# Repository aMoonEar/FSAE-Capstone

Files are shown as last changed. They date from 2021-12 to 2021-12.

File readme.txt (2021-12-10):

_________________________________________________________________

FSAE2 

Team Members:
Abdalaziz AlGhoul
Hisham Ali
Hasan Shazad
Munir Alsafi
Peter Saroufim

_________________________________________________________________

How to run the parametrization:

The parametrization can be ran from the MAIN.m file found in the MATLAB folder.
Running this program in MATLAB opens the GUI. The GUI has buttons to alter the input
parameters of the vehicle, alongside a button at the bottom of the GUI to re-generate
the vehicle assembly.

On the right of the GUI is an output log of the parameters that are calculated with the 
given inputs.

Once the dialog window claiming 'Successfully optimized' is shown, please re-build the solidworks
assembly to view the optimzed vehicle.

When the parameters are generated, the main differences can be found in the following assemblies

Solidworks\Steering\Updated Steering\Steering Rack and Pinion\Rack and Pinion

Solidworks\Suspension\SubAssemblies\Shock_Absorber_Assembly
Solidworks\Suspension\SubAssemblies\FLCALeft_Assembly
Solidworks\Suspension\SubAssemblies\FLCARight_Assembly
Solidworks\Suspension\SubAssemblies\FPushrod_Assembly
Solidworks\Suspension\SubAssemblies\FUCA_Assembly
Solidworks\Suspension\SubAssemblies\RLCALeft_Assembly
Solidworks\Suspension\SubAssemblies\RLCARight_Assembly
Solidworks\Suspension\SubAssemblies\RPushrod_Assembly

Solidworks\Chassis with Panels

_________________________________________________________________

Locations of Files:

[GroupFSAE2]
--> Log: Contains the output log while generating the updated design of the vehicle

--> MATLAB: Contains all of the programming code
-----> MAIN.m: Main matlab file that runs the GUI
-----> Subfunctions: Contains subfunctions that are used within the MAIN.m file

--> Reports: Contains all past written reports alongside the overleaf zips

--> Solidworks: Contains the main assembly and sub-assemblies
-----> Assembly.SLDASM: Main Vehicle assembly that gets updated with the parameters
-----> Equations: Contains the equation and parameters used in the solidworks parts
-----> Rest of the folders: Contains the subassemblies and parts

--> Excel Modelling: Contains the excel sheets used to model the vehicle

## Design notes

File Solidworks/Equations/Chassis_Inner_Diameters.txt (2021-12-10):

"Front_Hoop_ID"= 22.5mm

"D2@Sketch15"="Front_Hoop_ID"

"Front_Bulkhead_IW"= 22.2mm

"D4@Sketch18"="Front_Bulkhead_IW"

"Front_Bulkhead_SupportLower_IW"= 22.2mm

"D3@Sketch2"="Front_Bulkhead_SupportLower_IW"

"Front_Bulkhead_Bracing_ID"= 23mm

"D2@Sketch1"="Front_Bulkhead_Bracing_ID"

"D2@Sketch110"="Front_Bulkhead_Bracing_ID"

"Front_Bulkhead_Support_ID"= 23mm

"Side_Impact_Structure_ID"= 22.2mm

"D4@Sketch116" = "Side_Impact_Structure_ID"

"D2@Sketch119" = "Side_Impact_Structure_ID"

"Main_Hoop_Bracing_ID"= 23mm

"D2@Sketch120"="Main_Hoop_Bracing_ID"

"D2@Sketch121"="Main_Hoop_Bracing_ID"

"Rear_Bulkhead_ID"= 22.2mm

"D4@Sketch122"="Rear_Bulkhead_ID"

"D2@Sketch123"="Rear_Bulkhead_ID"

"Main_Hoop_ID"= 22.5mm

"D2@Sketch125"="Main_Hoop_ID"

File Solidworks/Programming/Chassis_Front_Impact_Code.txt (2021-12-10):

format long;

%Problem Characteristics
nnode = 18;                 %Number of Nodes
ndof_per_node = 3;          %Number of degrees of freedom per node
nnode_per_element = 2;      %Number of nodes per elements
nelem = 32;                 %Number of elements
nmat = 1;                   %Number of material types

%Elastic Modulus and Yield Stress of 4130 AISI Steel Tubes
Elastic_modulus = zeros(nmat,1);
Elastic_modulus(1,1) =  205000; %MPa

%Shear Modulus
Shear_modulus = zeros(nmat,1);
Shear_modulus(1,1) = 80000; %MPa

%Nodal coordinates in milimeters
Nodal_coordinates = zeros (nnode,2);

    %First line is the nodal coordinate is the x coordinate
    %Second line is the nodal coordinate is the y coordinate

Nodal_coordinates(1,1) = 0;
Nodal_coordinates(1,2) = 0;

Nodal_coordinates(2,1) = 0;
Nodal_coordinates(2,2) = 340;

Nodal_coordinates(3,1) = 439;
Nodal_coordinates(3,2) = 0;

Nodal_coordinates(4,1) = 451.66;
Nodal_coordinates(4,2) = 230;

Nodal_coordinates(5,1) = 463.78;
Nodal_coordinates(5,2) = 460.18;

Nodal_coordinates(6,1) = 878;
Nodal_coordinates(6,2) = 597.38;

Nodal_coordinates(7,1) = 878;
Nodal_coordinates(7,2) = 575.83;

Nodal_coordinates(8,1) = 878;
Nodal_coordinates(8,2) = 277;

Nodal_coordinates(9,1) = 878;
Nodal_coordinates(9,2) = 0;

Nodal_coordinates(10,1) = 1357;
Nodal_coordinates(10,2) = -51.5;

Nodal_coordinates(11,1) = 1836;
Nodal_coordinates(11,2) = -103;

Nodal_coordinates(12,1) = 1836;
Nodal_coordinates(12,2) = 275;

Nodal_coordinates(13,1) = 1836;
Nodal_coordinates(13,2) = 327.09;

Nodal_coordinates(14,1) = 1836;
Nodal_coordinates(14,2) = 1076;

Nodal_coordinates(15,1) = 2250.37;
Nodal_coordinates(15,2) = 276.37;

Nodal_coordinates(16,1) = 2249;
Nodal_coordinates(16,2) = -29;

Nodal_coordinates(17,1) = 2520;
Nodal_coordinates(17,2) = -29;

Nodal_coordinates(18,1) = 2520;
Nodal_coordinates(18,2) = 275;

%Connectivity table indicated the nodes that belong to each element
Connect_table = zeros(nelem,nnode_per_element + 1);

    %First line is node i that belongs to the element
    %Second line is node j that belongs to the element
    %Third line is the material flag
    
Connect_table(1,1) = 1;
Connect_table(1,2) = 2;
Connect_table(1,3) = 1;

Connect_table(2,1) = 2;
Connect_table(2,2) = 5;
Connect_table(2,3) = 1;

Connect_table(3,1) = 2;
Connect_table(3,2) = 4;
Connect_table(3,3) = 1;

Connect_table(4,1) = 1;
Connect_table(4,2) = 4;
Connect_table(4,3) = 1;

Connect_table(5,1) = 1;
Connect_table(5,2) = 3;
Connect_table(5,3) = 1;

Connect_table(6,1) = 5;
Connect_table(6,2) = 4;
Connect_table(6,3) = 1;

Connect_table(7,1) = 4;
Connect_table(7,2) = 3;
Connect_table(7,3) = 1;

Connect_table(8,1) = 5;
Connect_table(8,2) = 7;
Connect_table(8,3) = 1;

Connect_table(9,1) = 4;
Connect_table(9,2) = 7;
Connect_table(9,3) = 1;

Connect_table(10,1) = 4;
Connect_table(10,2) = 8;
Connect_table(10,3) = 1;

Connect_table(11,1) = 4;
Connect_table(11,2) = 9;
Connect_table(11,3) = 1;

Connect_table(12,1) = 3;
Connect_table(12,2) = 9;
Connect_table(12,3) = 1;

Connect_table(13,1) = 7;
Connect_table(13,2) = 6;
Connect_table(13,3) = 1;

Connect_table(14,1) = 7;
Connect_table(14,2) = 8;
Connect_table(14,3) = 1;

Connect_table(15,1) = 8;
Connect_table(15,2) = 9;
Connect_table(15,3) = 1;

Connect_table(16,1) = 7;
Connect_table(16,2) = 12;
Connect_table(16,3) = 1;

Connect_table(17,1) = 8;
Connect_table(17,2) = 12;
Connect_table(17,3) = 1;

Connect_table(18,1) = 9;
Connect_table(18,2) = 12;
Connect_table(18,3) = 1;

Connect_table(19,1) = 9;
Connect_table(19,2) = 10;
Connect_table(19,3) = 1;

Connect_table(20,1) = 10;
Connect_table(20,2) = 11;
Connect_table(20,3) = 1;

Connect_table(21,1) = 11;
Connect_table(21,2) = 12;
Connect_table(21,3) = 1;

Connect_table(22,1) = 12;
Connect_table(22,2) = 13;
Connect_table(22,3) = 1;

Connect_table(23,1) = 13;
Connect_table(23,2) = 14;
Connect_table(23,3) = 1;

Connect_table(24,1) = 14;
Connect_table(24,2) = 15;
Connect_table(24,3) = 1;

Connect_table(25,1) = 12;
Connect_table(25,2) = 15;
Connect_table(25,3) = 1;

Connect_table(26,1) = 11;
Connect_table(26,2) = 15;
Connect_table(26,3) = 1;

Connect_table(27,1) = 11;
Connect_table(27,2) = 16;
Connect_table(27,3) = 1;

Connect_table(28,1) = 15;
Connect_table(28,2) = 16;
Connect_table(28,3) = 1;

Connect_table(29,1) = 16;
Connect_table(29,2) = 17;
Connect_table(29,3) = 1;

Connect_table(30,1) = 15;
Connect_table(30,2) = 17;
Connect_table(30,3) = 1;

Connect_table(31,1) = 15;
Connect_table(31,2) = 18;
Connect_table(31,3) = 1;

Connect_table(32,1) = 17;
Connect_table(32,2) = 18;
Connect_table(32,3) = 1;

%Radii of tubes in mm
OutterradiustubeA = 12.5;
InnerradiustubeA = (12.5 - 1.25)-4;

OutterradiustubeB = 12.7;
InnerradiustubeB = (12.7 - 1.6);

%Width of sqaure tubes in mm
OutterWidthtubeB = 25.4;
InnerWidthtubeB = (25.4-3.2)-4;

%Moment of inertia of tubes (I)
InertiaPipeA = (pi/4)*((OutterradiustubeA^4)-(InnerradiustubeA^4));
InertiaPipeB = (pi/4)*((OutterradiustubeB^4)-(InnerradiustubeB^4));
InertiaSquareB = ((OutterWidthtubeB^4)/12)-((InnerWidthtubeB^4)/12);

%Polar moment of inertia of tubes (J)
PolarpipeA = (pi/2)*((OutterradiustubeA^4)-(InnerradiustubeA^4));
PolarpipeB = (pi/2)*((OutterradiustubeB^4)-(InnerradiustubeB^4));
PolarsquareB = ((OutterWidthtubeB^4)/6)-((InnerWidthtubeB^4)/6);

%Assigning an outer radius to each element
Tube_outer_radius = zeros(nelem,nmat);
Tube_outer_radius(1,1) = OutterradiustubeB;
Tube_outer_radius(2,1) = OutterradiustubeB;
Tube_outer_radius(3,1) = OutterradiustubeB;
Tube_outer_radius(4,1) = OutterradiustubeB;
Tube_outer_radius(5,1) = OutterWidthtubeB;
Tube_outer_radius(6,1) = OutterradiustubeB;
Tube_outer_radius(7,1) = OutterradiustubeB;
Tube_outer_radius(8,1) = OutterradiustubeB;
Tube_outer_radius(9,1) = OutterradiustubeB;
Tube_outer_radius(10,1) = OutterradiustubeB;
Tube_outer_radius(11,1) = OutterradiustubeB;
Tube_outer_radius(12,1) = OutterWidthtubeB;
Tube_outer_radius(13,1) = OutterradiustubeA;
Tube_outer_radius(14,1) = OutterradiustubeA;
Tube_outer_radius(15,1) = OutterradiustubeA;
Tube_outer_radius(16,1) = OutterradiustubeB;
Tube_outer_radius(17,1) = OutterradiustubeB;
Tube_outer_radius(18,1) = OutterradiustubeB;
Tube_outer_radius(19,1) = OutterWidthtubeB;
Tube_outer_radius(20,1) = OutterWidthtubeB;
Tube_outer_radius(21,1) = OutterradiustubeA;
Tube_outer_radius(22,1) = OutterradiustubeA;
Tube_outer_radius(23,1) = OutterradiustubeA;
Tube_outer_radius(24,1) = OutterradiustubeB;
Tube_outer_radius(25,1) = OutterradiustubeB;
Tube_outer_radius(26,1) = OutterradiustubeB;
Tube_outer_radius(27,1) = OutterWidthtubeB;
Tube_outer_radius(28,1) = OutterradiustubeB;
Tube_outer_radius(29,1) = OutterWidthtubeB;
Tube_outer_radius(30,1) = OutterradiustubeB;
Tube_outer_radius(31,1) = OutterradiustubeB;
Tube_outer_radius(32,1) = OutterradiustubeB;

%Assigning an inner radius to each element
Tube_inner_radius = zeros(nelem,nmat);
Tube_inner_radius(1,1) = InnerradiustubeB;
Tube_inner_radius(2,1) = InnerradiustubeB;
Tube_inner_radius(3,1) = InnerradiustubeB;
Tube_inner_radius(4,1) = InnerradiustubeB;
Tube_inner_radius(5,1) = InnerWidthtubeB;
Tube_inner_radius(6,1) = InnerradiustubeB;
Tube_inner_radius(7,1) = InnerradiustubeB;
Tube_inner_radius(8,1) = InnerradiustubeB;
Tube_inner_radius(9,1) = InnerradiustubeB;
Tube_inner_radius(10,1) = InnerradiustubeB;
Tube_inner_radius(11,1) = InnerradiustubeB;
Tube_inner_radius(12,1) = InnerWidthtubeB;
Tube_inner_radius(13,1) = InnerradiustubeA;
Tube_inner_radius(14,1) = InnerradiustubeA;
Tube_inner_radius(15,1) = InnerradiustubeA;
Tube_inner_radius(16,1) = InnerradiustubeB;
Tube_inner_radius(17,1) = InnerradiustubeB;
Tube_inner_radius(18,1) = InnerradiustubeB;
Tube_inner_radius(19,1) = InnerWidthtubeB;
Tube_inner_radius(20,1) = InnerWidthtubeB;
Tube_inner_radius(21,1) = InnerradiustubeA;
Tube_inner_radius(22,1) = InnerradiustubeA;
Tube_inner_radius(23,1) = InnerradiustubeA;
Tube_inner_radius(24,1) = InnerradiustubeB;
Tube_inner_radius(25,1) = InnerradiustubeB;
Tube_inner_radius(26,1) = InnerradiustubeB;
Tube_inner_radius(27,1) = InnerWidthtubeB;
Tube_inner_radius(28,1) = InnerradiustubeB;
Tube_inner_radius(29,1) = InnerWidthtubeB;
Tube_inner_radius(30,1) = InnerradiustubeB;
Tube_inner_radius(31,1) = InnerradiustubeB;
Tube_inner_radius(32,1) = InnerradiustubeB;

%Assigning a moment of inertia to every element
Tube_inertia = zeros(nelem,nmat);
Tube_inertia(1,1) = InertiaPipeB;
Tube_inertia(2,1) = InertiaPipeB;
Tube_inertia(3,1) = InertiaPipeB;
Tube_inertia(4,1) = InertiaPipeB;
Tube_inertia(5,1) = InertiaSquareB;
Tube_inertia(6,1) = InertiaPipeB;
Tube_inertia(7,1) = InertiaPipeB;
Tube_inertia(8,1) = InertiaPipeB;
Tube_inertia(9,1) = InertiaPipeB;
Tube_inertia(10,1) = InertiaPipeB;
Tube_inertia(11,1) = InertiaPipeB;
Tube_inertia(12,1) = InertiaSquareB;
Tube_inertia(13,1) = InertiaPipeA;
Tube_inertia(14,1) = InertiaPipeA;
Tube_inertia(15,1) = InertiaPipeA;
Tube_inertia(16,1) = InertiaPipeB;
Tube_inertia(17,1) = InertiaPipeB;
Tube_inertia(18,1) = InertiaPipeB;
Tube_inertia(19,1) = InertiaSquareB;
Tube_inertia(20,1) = InertiaSquareB;
Tube_inertia(21,1) = InertiaPipeA;
Tube_inertia(22,1) = InertiaPipeA;
Tube_inertia(23,1) = InertiaPipeA;
Tube_inertia(24,1) = InertiaPipeB;
Tube_inertia(25,1) = InertiaPipeB;
Tube_inertia(26,1) = InertiaPipeB;
Tube_inertia(27,1) = InertiaSquareB;
Tube_inertia(28,1) = InertiaPipeB;
Tube_inertia(29,1) = InertiaSquareB;
Tube_inertia(30,1) = InertiaPipeB;
Tube_inertia(31,1) = InertiaPipeB;
Tube_inertia(32,1) = InertiaPipeB;

%Assigning a polar moment of inertia to every element
Tube_polar = zeros(nelem,nmat);
Tube_polar(1,1) = PolarpipeB;
Tube_polar(2,1) = PolarpipeB;
Tube_polar(3,1) = PolarpipeB;
Tube_polar(4,1) = PolarpipeB;
Tube_polar(5,1) = PolarsquareB;
Tube_polar(6,1) = PolarpipeB;
Tube_polar(7,1) = PolarpipeB;
Tube_polar(8,1) = PolarpipeB;
Tube_polar(9,1) = PolarpipeB;
Tube_polar(10,1) = PolarpipeB;
Tube_polar(11,1) = PolarpipeB;
Tube_polar(12,1) = PolarsquareB;
Tube_polar(13,1) = PolarpipeA;
Tube_polar(14,1) = PolarpipeA;
Tube_polar(15,1) = PolarpipeA;
Tube_polar(16,1) = PolarpipeB;
Tube_polar(17,1) = PolarpipeB;
Tube_polar(18,1) = PolarpipeB;
Tube_polar(19,1) = PolarsquareB;
Tube_polar(20,1) = PolarsquareB;
Tube_polar(21,1) = PolarpipeA;
Tube_polar(22,1) = PolarpipeA;
Tube_polar(23,1) = PolarpipeA;
Tube_polar(24,1) = PolarpipeB;
Tube_polar(25,1) = PolarpipeB;
Tube_polar(26,1) = PolarpipeB;
Tube_polar(27,1) = PolarsquareB;
Tube_polar(28,1) = PolarpipeB;
Tube_polar(29,1) = PolarsquareB;
Tube_polar(30,1) = PolarpipeB;
Tube_polar(31,1) = PolarpipeB;
Tube_polar(32,1) = PolarpipeB;

%Local stiffness matrices
Keloc = Local_stiffness(Nodal_coordinates,Connect_table,Tube_outer_radius,Tube_inner_radius,Tube_inertia,Tube_polar,Elastic_modulus,Shear_modulus);

%Rotation matrices to switch between local and global coordinates
R = Rotation(Nodal_coordinates,Connect_table);

%Global stiffness matrices
Ke = Global_stiffness(Keloc,R);

%Assemblage matrix
Ka = Assemblage_matrix(nnode,ndof_per_node,Connect_table,Ke);

%External force vector
Fa = zeros(nnode*ndof_per_node,1);

Frontimpact = -18245.833; %Newtons
Fa(1,1) = (Frontimpact/4);
Fa(4,1) = (Frontimpact/4);

%Gravitational Force from Driver
Fa(29,1) = 100*9.8;
Fa(32,1) = 100*9.8;

%Boundary conditions appropiate for a front impact test
BC = zeros(nnode,ndof_per_node);

%fix the rear bulkhead, 1 means fixed
BC(17,1:3) = 1;
BC(18,1:3) = 1;

% Modifying Ka into KaSol and Fa into FaSol to get solution 
  beta = max(max(Ka))*10e9;
  KaSol = Ka;
  FaSol = Fa;
  for i = 1:nnode
    for j = 1:ndof_per_node
      if BC(i,j) == 1
        KaSol((i-1)*ndof_per_node + j,(i-1)*ndof_per_node + j) = Ka((i-1)*ndof_per_node + j,(i-1)*ndof_per_node + j) + beta;
        FaSol((i-1)*ndof_per_node + j,1) = beta*0;
      end
    end
  end

%Global displacement calculation

U = KaSol\FaSol;

%Processing of result
Reaction_forces = [];
Ulocal = zeros(2*ndof_per_node,nelem);
Uglobal = zeros(2*ndof_per_node,nelem);
Flocal = zeros(2*ndof_per_node,nelem);
axial_stress = zeros(nelem,1);

Ua = U;
Fa = Ka*Ua;
x = 1;
for i = 1:nnode
    for j = 1:ndof_per_node
        if BC(i,j)==1
            Reaction_forces(x,1) = Fa((i-1)*ndof_per_node + j,1);
            x = x+1;
        end
    end
end

%Parameters to be used when calcu lating the stiffness matrices
A = Cross_sectional_of_element(Tube_outer_radius,Tube_inner_radius);
L = Length_of_elements(Nodal_coordinates,Connect_table);
E = Elastic_modulus_of_elements(Elastic_modulus,Connect_table);
G = Shear_modulus_of_elements(Shear_modulus,Connect_table);
I = Moment_Inertia_of_elements(Tube_inertia);
J = Polar_moment_of_inertia(Tube_polar);
Kglobal = Global_stiffness(Keloc,R);
%Rotating local displacement and external force vectors to global coordinates
for i = 1:nelem     
     Rot = R(:,:,i);
     for j = 1:ndof_per_node
       Uglobal(j,i) = Ua((Connect_table(i,1) - 1)*ndof_per_node + j,1);
       Uglobal(ndof_per_node + j,i) = Ua((Connect_table(i,2) - 1)*ndof_per_node + j,1);  
     end
     Ulocal(:,i) = Rot*Uglobal(:,i);
     Flocal(:,i) = Keloc(:,:,i)*Ulocal(:,i);
    %calculating stresses in each element
    axial_stress(i,1) = max(Flocal(2,i))/A(i,1); %axial stress
    shear_stress_yaxis(i,1) = (max(Flocal(1,i)))/A(i,1); %y axis shear stress
    torsional_stress(i,1) = (max(Flocal(3,i))*Tube_outer_radius(i,1))/Tube_polar(i,1); %Torsional stress
    bending_stress_yaxis(i,1) = (max(Flocal(3,i))*Tube_outer_radius(i,1))/Tube_inertia(i,1); %Bending stress y axis
end

%Oraganizing required stresses in a vector
stresses = zeros(1,4);

stresses(1,1) = max(axial_stress); %Tensile stress
stresses(1,2) = max(abs(shear_stress_yaxis(i,1))); %x Shear stress
stresses(1,3) = max(abs(torsional_stress(i,1))); %Torsional stress
stresses(1,4) = max(abs(bending_stress_yaxis(i,1))); %z Bending stress

%Calculating safety factors and organizing in a vector
SF = zeros(1,4);

SF(1,1) = abs(435/(stresses(1,1))); %Axial stress safety factor
SF(1,2) = 435/stresses(1,2); %Y Shear Stress safety factor
SF(1,3) = 435/stresses(1,3); %Torsional Stress safety factor
SF(1,4) = 435/stresses(1,4); %Y Bending Stress safety factor

disp(min(SF));

%Calculating the parameter that are used to calculate the stiffness matrix
%Area of element calculation
function A = Cross_sectional_of_element(Tube_outer_radius,Tube_inner_radius)
    [nelem,~] = size(Tube_inner_radius);
    A = zeros(nelem,1);
    for i = 1:nelem
        A(i,1) = pi*((Tube_outer_radius(i,1)^2)-(Tube_inner_radius(i,1)^2));
    end
end

function L = Length_of_elements(Nodal_coordinates,Connect_table)
    [nelem,~] = size(Connect_table);
    L = zeros(nelem,1);
    for i = 1:nelem
        L(i,1) = sqrt((Nodal_coordinates(Connect_table(i,1),1) - Nodal_coordinates(Connect_table(i,2),1))^2 + (Nodal_coordinates(Connect_table(i,1),2) - Nodal_coordinates(Connect_table(i,2),2))^2);
    end
end

%Elastic modulus of elements
function E = Elastic_modulus_of_elements(Elastic_modulus,Connect_table)
    [nelem,~] = size(Connect_table);
    E = zeros(nelem,1);
   for i = 1:nelem
    E(i,1) = Elastic_modulus(1,1);
   end
end

%Shear modulus of elements
function G = Shear_modulus_of_elements(Shear_modulus,Connect_table)
    [nelem,~] = size(Connect_table);
    G = zeros(nelem,1);
    for i = 1:nelem
    G(i,1) = Shear_modulus(1,1);
   end 
end

%Moment of inertia of elements
function I = Moment_Inertia_of_elements(Tube_inertia)
    [nelem,~] = size(Tube_inertia);
    I = zeros(nelem,1);
    for i = 1:nelem
            I(i,1) = Tube_inertia(i,1);
     end
end

%Polar moment of Inertia of elements
function J = Polar_moment_of_inertia(Tube_polar)
    [nelem,~] = size(Tube_polar);
    J = zeros(nelem,1);
    for i = 1:nelem
            J(i,1) = Tube_polar(i,1);
     end
end

%3D Local stiffness matrix calculation
function Keloc = Local_stiffness(Nodal_coordinates,Connect_table,Tube_outer_radius,Tube_inner_radius,Tube_inertia,Tube_polar,Elastic_modulus,Shear_modulus)
    [nelem,~] = size(Connect_table);
    Keloc = zeros(6,6,nelem); %each element is characterized by a 12x12 matrix
   
    A = Cross_sectional_of_element(Tube_outer_radius,Tube_inner_radius);
    L = Length_of_elements(Nodal_coordinates,Connect_table);
    E = Elastic_modulus_of_elements(Elastic_modulus,Connect_table);
    G = Shear_modulus_of_elements(Shear_modulus,Connect_table);
    I = Moment_Inertia_of_elements(Tube_inertia);
    J = Polar_moment_of_inertia(Tube_polar);
    
    for i = 1:nelem
       
        %first row
    Keloc(1,1,i) = (A(i,1)*E(i,1))/L(i,1);
    Keloc(1,4,i) = -(A(i,1)*E(i,1))/L(i,1);  
   
    %second row
    Keloc(2,2,i) = (12*E(i,1)*I(i,1))/L(i,1)^3;
    Keloc(2,3,i) = (6*E(i,1)*I(i,1))/L(i,1)^2;
    Keloc(2,5,i) = -Keloc(2,2,i);
    Keloc(2,6,i) = Keloc(2,3,i);
    
    %third row
    Keloc(3,2,i) = (6*E(i,1)*I(i,1))/L(i,1)^2;
    Keloc(3,3,i) = (4*E(i,1)*I(i,1))/L(i,1);
    Keloc(3,5,i) = -Keloc(3,2,i);
    Keloc(3,6,i) = Keloc(3,3,i)/2;
    
    %fourth row
    Keloc(4,1,i) = -(A(i,1)*E(i,1))/L(i,1);
    Keloc(4,4,i) = (A(i,1)*E(i,1))/L(i,1);
    
    %fifth row
    Keloc(5,2,i) = -(12*E(i,1)*I(i,1))/L(i,1)^3;
    Keloc(5,3,i) = -(6*E(i,1)*I(i,1))/L(i,1)^2;
    Keloc(5,5,i) = -Keloc(6,2,i);
    Keloc(5,6,i) = Keloc(6,3,i);
    
    %sixth row
    Keloc(6,2,i) = (6*E(i,1)*I(i,1))/L(i,1)^2;
    Keloc(6,3,i) = (2*E(i,1)*I(i,1))/L(i,1);
    Keloc(6,5,i) = -Keloc(3,2,i);
    Keloc(6,6,i) = Keloc(3,3,i)*2;
    end
end

function R = Rotation(Nodal_coordinates,Connect_table)
  [nelem,~] = size(Connect_table);
  R = zeros(6,6,nelem);
  L = Length_of_elements(Nodal_coordinates,Connect_table);
  for i = 1:nelem
    %l
    R(1,1,i) = (Nodal_coordinates(Connect_table(i,2),1) - Nodal_coordinates(Connect_table(i,1),1)/L(i,1));
    %m
    R(1,2,i) = (Nodal_coordinates(Connect_table(i,2),2) - Nodal_coordinates(Connect_table(i,1),2)/L(i,1));
    R(2,1,i) = -R(1,2,i);
    R(2,2,i) = R(1,1,i);
    R(3,3,i) = 1;   
    R(4,4,i) = R(1,1,i);
    R(4,5,i) = R(1,2,i);
    R(5,4,i) = -R(1,2,i);
    R(5,5,i) = R(1,1,i);
    R(6,6,i) = 1;
    R(:,:,i) = R(:,:,i)/L(i,1);     
  end
end

%Global stiffness matrix calculation
function Kglobal = Global_stiffness(Keloc,R)
    [sizeKglobal,~,nelem]=size(Keloc);
    Kglobal = zeros(sizeKglobal,sizeKglobal,nelem);
    for i = 1:nelem
        Rotate = R(:,:,i);
        Kglobal(:,:,i) = Rotate'*Keloc(:,:,i)*Rotate;
    end
end

function Ka =  Assemblage_matrix(nnode,ndof_per_node,Connect_table,Kglobal)
    Ka = zeros(nnode*ndof_per_node,nnode*ndof_per_node);
    [~,~,nelem]=size(Kglobal);
     for ii = 1:nnode
        for jj = 1:nnode
            for k = 1:nelem
                if ii == Connect_table(k,1) && jj == Connect_table(k,1)
                    for i = 1:ndof_per_node
                        for j = 1:ndof_per_node
                            Ka((ii - 1)*ndof_per_node + i,(jj - 1)*ndof_per_node + j) = Ka((ii - 1)*ndof_per_node + i,(jj - 1)*ndof_per_node + j) + Kglobal(i,j,k);
                        end
                    end
                elseif ii == Connect_table(k,2) && jj == Connect_table(k,2)
                    for i = 1:ndof_per_node
                        for j = 1:ndof_per_node
                            Ka((ii - 1)*ndof_per_node + i,(jj - 1)*ndof_per_node + j) = Ka((ii - 1)*ndof_per_node + i,(jj - 1)*ndof_per_node + j) + Kglobal(i + ndof_per_node,j + ndof_per_node,k);
                        end
                    end
                elseif ii == Connect_table(k,1) && jj == Connect_table(k,2)
                    for i = 1:ndof_per_node
                        for j = 1:ndof_per_node
                            Ka((ii - 1)*ndof_per_node + i,(jj - 1)*ndof_per_node + j) = Ka((ii - 1)*ndof_per_node + i,(jj - 1)*ndof_per_node + j) + Kglobal(i,j + ndof_per_node,k);
                        end
                    end
                elseif ii == Connect_table(k,2) && jj == Connect_table(k,1)
                    for i = 1:ndof_per_node
                        for j = 1:ndof_per_node
                            Ka((ii - 1)*ndof_per_node + i,(jj - 1)*ndof_per_node + j) = Ka((ii - 1)*ndof_per_node + i,(jj - 1)*ndof_per_node + j) + Kglobal(i + ndof_per_node,j,k);
                        end
                    end
                end
            end
        end            
     end
end

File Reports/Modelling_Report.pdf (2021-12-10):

# MCG 4322[A]

# FSAE Modelling Report

# FSAE 2

by

### AbdalAziz AlGhoul (300005268)

### Hasan Shahzad (300001167)

### Hisham Ali (300010128)

### Peter Saroufim (300015864)

### Munir Alsafi (300013845)

University of Ottawa

Department of Mechanical Engineering

October 6, 2021

Professor: Mihaita Matei

Design TA: Nathaniel Mailhot

Marking TA: Ahmed Taimah

# Table of Contents

List of Figures | v
1 Project Charter | 1
2 Design Solution | 5
3 Geometric Relations & Properties | 12

ii

4 Kinematics and Applied Forces | 17
4.2 Steady State Low Speed Cornering Geometry and Vehicle Turning Radius | 18
References | 38
APPENDICES | 40
A Data Sheets | 41

iii

B Additional material | 44

iv

# List of Figures

2.1 Updated Solution of the vehicle with labeled components | | 5
2.2 Updated Solution of the vehicle with dimensions | | 6

3.1 Anti-squat Geometry (left red line) and Anti-dive Geometry (right red line) 14

3.2 Suspension Geometry to Locate Instantaneous Points and Roll Centre . . . | 16
4.1 2-D Kinematic Model of Vehicle | | 18
4.2 Vehicle Steering Ackermann Method | | 19
4.3 FBD of Car on a Level Road | | 20
4.4 FBD of Car on an Inclined Road | | 21
4.5 FBD of Car on a Banked Road | | 22
4.6 FBD of an Accelerating Car on a Level Road | | 24
4.7 FBD of an Accelerating Car on an Inclined Road | | 25
4.8 Reaction at Wheels Due to Applied Centripetal Force | | 27
4.9 FBD of the maximum force exerted by the driver on the brake pedal . . . | 28
4.10 FBD of the balance bar and the two master brake cylinders | | 29
4.11 FBD of one master cylinder and the two calipers | | 30
4.12 FBD of the caliper and rotor | | | 30
4.13 FBD of the wheel on the road | | 31
4.14 Slip Angle Representation | | 33
4.15 FBD for forces acting on the vehicle | | 36
| v

A.1 Data Sheet for Sony VTC6 Battery Cell (1) | | 41
A.2 Data Sheet for Sony VTC6 Battery Cell (2) | | 42
A.3 Data Sheet for Emrax 228 Motor | | 43

vi

# Chapter 1

# Project Charter

## 1.1 Mandate

Formula SAE (Society of Automotive Engineers) is a series of international competitions in

which university teams compete to design and manufacture the best performing race cars.

Our design team has been approached by a car manufacturer and contracted to develop

a small electric Formula-style race car. The prototype should have high performance and

be sufficiently durable to successfully complete all the static and dynamic events at the

Formula SAE competitions. The prototype will be evaluated as it must follow all Formula

SAE rules and regulations.

## 1.2 Requirements

1. The tractive system must be completely isolated from the chassis and any other

conductive parts of the vehicle.

2. The tractive system motor(s) must be connected to the accumulator through a motor

controller.

3. Only electrical motors of any type are allowed and the number of motors is not

limited.

4. All accumulator containers must be designed to withstand forces from deceleration

in all directions.

1

Group FSAE 2 | Modelling Report
5. The accumulator container(s) must be completely closed at all times without the

need to install extra protective covers.

6. Exposed high speed final drivetrain equipment must be fitted with scatter shields

that may be composed of multiple pieces.

7. Coolant for electric motors and accumulators must be either plain water with no

additives or oil.

8. The braking system must be operated by a single control and act on all four wheels.

It must have two independent hydraulic circuits that have their own fluid reserve.

9. Vehicles may have either dry or wet tires.
10. The steering wheel must be mechanically connected to the front wheels.
11. The chassis must include both a main hoop and a front hoop.

## 1.3 Constraints

1. The maximum power drawn from the accumulator must not exceed 80 kW.
2. The maximum permitted voltage that may occur between any two points must not

exceed 600 V DC.

3. A maximum of 12 kg is allowed in any accumulator container section.
4. Regenerating energy is allowed and unrestricted when the vehicle speed is more than 5 km/hr.
5. The brake pedal and system must withstand a minimum force of 2000 N
6. Wheels must be 203.2 mm (8.0 inches) or more in diameter.

Page 2

Group FSAE 2 | Modelling Report
7. The vehicle must be equipped with an operational suspension system with usable

wheel travel of at least 50 mm, with a driver seated.

## 1.4 Criteria

1. Performance: Increase in handling, response, and tractive capability of the steering,

suspension, and tires. Increase in acceleration and traction force of the vehicle.

2. Serviceability: Ease of repair, subsystems accessibility, parts interchangeability,

low manufacturing complexity, and standardization of fasteners across the vehicle.

3. Safety: Visibility, cockpit protection, firewall, rollover protection, and scatter shields.

Wiring is safely routed, color coded, and marked for function.

4. Ergonomics: Driver comfort, arm room, leg room, head restraint, ease of control,

seat adjustability, and readability of essential instruments.

5. Reliability: Consistent and reliable braking system, drivetrain, and motor.
6. Aerodynamics: Drag reduction, lift reduction, noise elimination, and downforce

gain.

7. Cost: Raw material selection, manufacturing process selection, and design optimiza-

tions for simpler solutions.

8. Efficiency: Lightweight design, increase in range, and improve in performance and

structural integrity.

## 1.5 Parameterization Outline

The design of the vehicle is driven by the length and weight to be able to accommodate

drivers of sizes ranging from 5th percentile female up to 95th percentile male. Accommo-

Page 3

Group FSAE 2 | Modelling Report

dation will include driver position, driver controls, and driver equipment. Primarily, the

wheel base will be altered to change the length and weight of the vehicle to accommodate

the driver. To alter the wheel base, the geometrical properties of the space frame and its

members will be adjusted and hence, the overall weight of the vehicle will vary.

Page 4

# Chapter 2

# Design Solution

## 2.1 Updated Solution

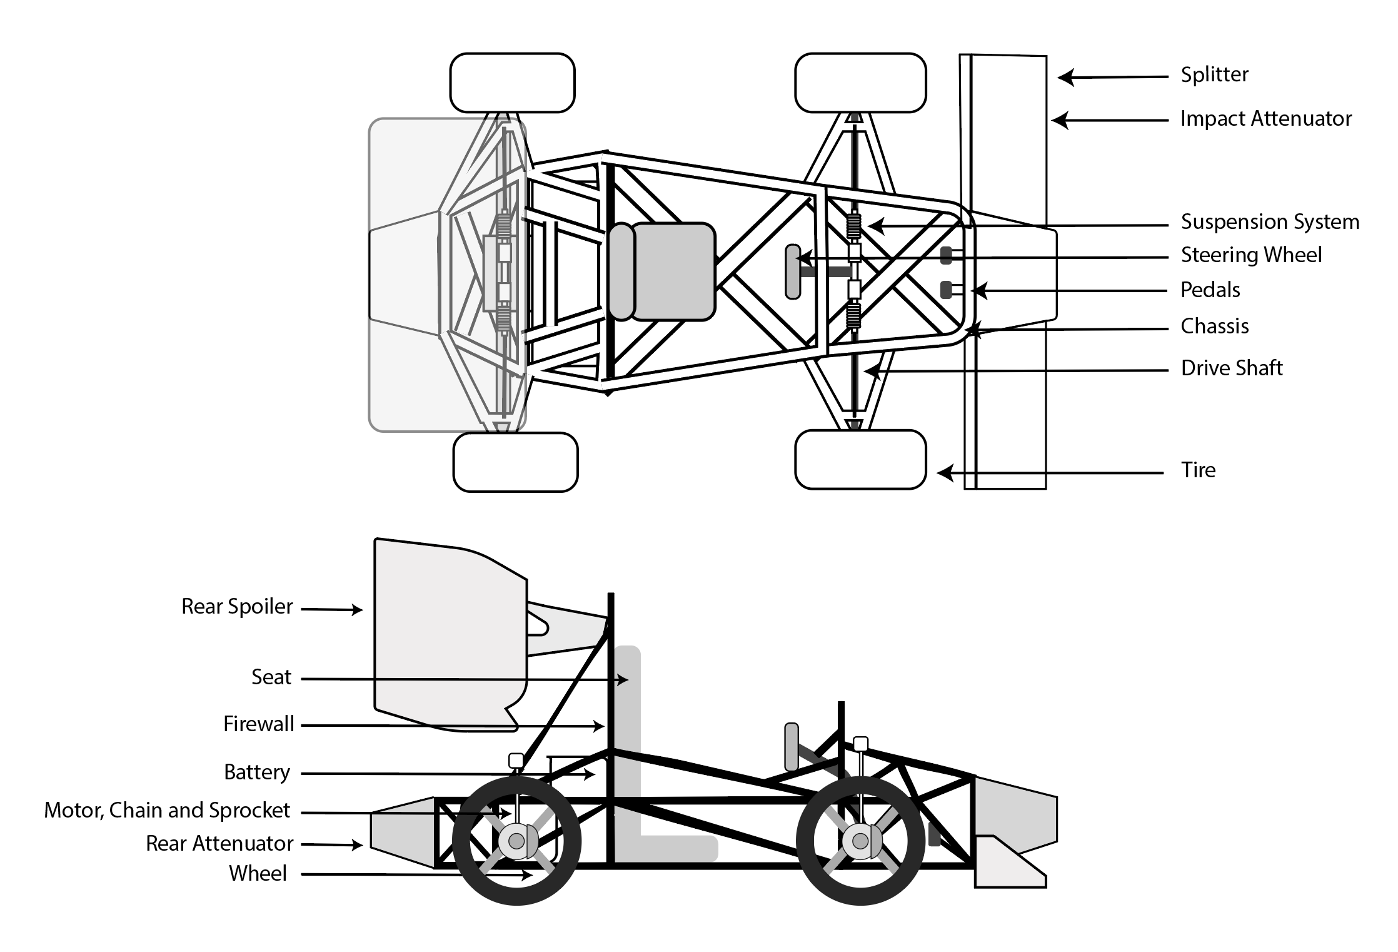
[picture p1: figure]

Figure 2.1: Updated Solution of the vehicle with labeled components

5

Group FSAE 2 | Modelling Report

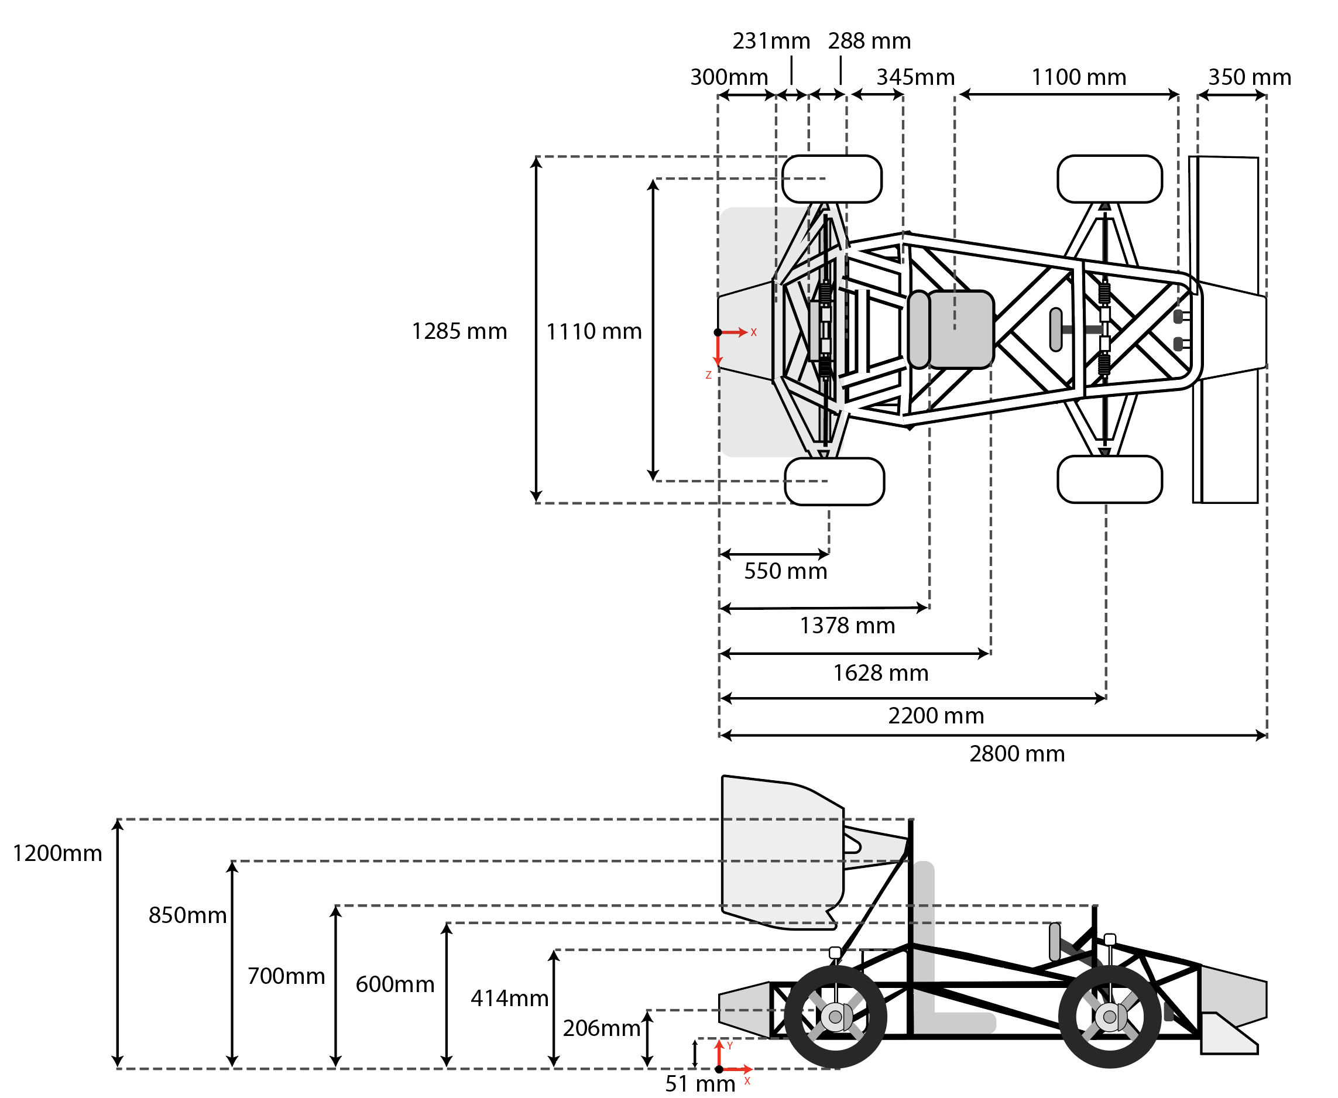
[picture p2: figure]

Figure 2.2: Updated Solution of the vehicle with dimensions

The updated design of the FSAE car is shown in figure 2.1 and figure 2.2 is based on the

decision criteria tables in the Concept Report. Additional design concepts include a rear

spoiler and a front splitter which will improve the aerodynamic performance of the car.

Furthermore, the tripod joints that couple the motor shaft and axle half shaft are going to

be replaced with CV joints as they are less expensive to purchase and maintain.

Page 6

Group FSAE 2 | Modelling Report

## 2.2 Approximations

### 2.2.1 Vehicle Assumptions

Table 2.1: Assumptions of vehicle operation

Parameter | Approximation
Maximum Speed | 105 km/h
Maximum Acceleration | 6 m/s²
Maximum Force Applied on the Brake Pedal | 2000 N
Average Impact Deceleration | 196 m/s²

### 2.2.2 Mass Approximations

Table 2.2: Weight Calculation of the Vehicle Approximation [1]

Item | Weight (kg)
Steel Spaceframe | 31.80
Maximum Driver Weight | 111.58
Front Attenuator | 1
Front Wing | 3.10
Rear Wing | 2.80

Page 7

Group FSAE 2 | Modelling Report
Wing Mounting | 1.32
Battery | 32
Emraxx 228 Motor | 12
Chain and Sprocket Kit | 3.60
Motor Mount | 0.17
Limited Slip Differential | 2.60
Chain and Sprocket Kit | 3.58
Half Axle Shaft | 0.7
Tripod Joints | 0.2
Front Control Arm Assemblies | 2.6
Rear Control Arm Assemblies | 2.4
Front Uprights | 1.8
Rear Uprights | 8.1
Rockers Assemblies | 1.8
Shock Absorber | 2.6
Swaybar Assemblies | 0.6
Rotors | 1.22
Breakline Assembly | 2.8

Page 8

Group FSAE 2 | Modelling Report
Break Pads | 0.2
Break Calipers | 0.85
Rack and Pinion Subsystem | 3.1
Steering Wheel | 1.97
Quick Release | 0.99
Steering Shaft | 2.2
Intermediate shaft | 0.82
Steering column bushing | 1.09
Tie rod | 0.63
Tires | 17.96
Wheels | 13.3
Front Wheel Hubs | 2.4
Rear Wheel Hubs | 10.4
Wiring and Instruments | 2.3
Seat | 2.07
Firewall | 2.02
Harness | 1.04
Throttle and Brake Pedal System | 2.4

Page 9

Group FSAE 2 | Modelling Report
Total Mass of the Car | 297

### 2.2.3 Accumulator Approximations

It is important that the accumulator parameters are estimated so that the geometric and

mass properties of the vehicle can be calculated. The table below illustrates the approx-

imate dimensions and weight of the battery. The calculations for how this model was

calculated are illustrated in appendix B.1

Table 2.3: Sony VTC6 Battery Specification [2]

Parameter | Value
Continuous Max. Discharge (A) | 15.0
Peak Max. Discharge (A) | 30.0
Nominal Voltage (V) | 3.6
Max Voltage (V) | 4.2
Capacity (Ah) | 3.0
Diameter (mm) | 18.3
Height (mm) | 65.0
Mass (g) | 48.0

Page 10

Group FSAE 2 | Modelling Report

Table 2.4: Sony VTC6 Accumulator Design 5 sections connected in series consisting of (4px28s)

Parameter | Value
Capacity per Module (Ah) | 12
Nominal Voltage per Module (V) | 100.8
Nominal Capacity per Module (Wh) | 1209.6
Peak Voltage per Module (V) | 117.6
Peak Capacity per Module (Wh) | 1411.2
Total Nominal Voltage (V) | 504
Accumulator Peak Voltage (V) | 588
Max Discharge Current (A) | 120
Accumulator Peak Power (W) | 70560
Accumulator Capacity (kWh) | 6.048
Dimensions X (mm) | 693.4
Dimensions Y (mm) | 345
Dimensions Z (mm) | 123.2
Weight (Batteries) (kg) | 26.88
Accumulator Estimated Weight (kg) | 30.38

Page 11

# Chapter 3

# Geometric Relations & Properties

## 3.1 Wheelbase to Track Ratio

The wheelbase to track ratio is a mathematical relationship that characterizes the handling

of the vehicle. The track width determines the weight that is transferred by the mass of

the car in cornering. The wheelbase determines how much weight is transferred by the

mass of the car in acceleration and braking.

Wheelbase Length
Track Length =

1650mm
1110mm
= 1.49 | (3.1)

The FSAE car’s wheelbase length is designed to be 1650 mm while the track width

is the 1110 mm, giving a ratio of 1.49. This ratio nearly falls into the range of optimum

ratio which is 1.5 to 1.7. An optimum ratio of wheelbase to track ensures proper mass

distribution throughout the car, resulting in high handling performance.

## 3.2 Center of Mass Calculation

A vehicle’s center of mass is the point where the sum of all of the subassembly masses act.

The center of mass is used to determine overall forces when the car is turning, accelerating

or decelerating. Most FSAE vehicles are designed to have a relatively low center of mass.

To measure the center of mass of the car, the subassemblies were split into volumes. Each

volume had its own center of mass which was approximated using the dimensions and the origin in the table below [3].

12

Group FSAE 2 | Modelling Report

Table 3.1: Volumes and their Respective Approximate Center of Mass

Volume | Weight (kg) | x - Coordinate (mm) | y - Coordinate (mm) | z - coordinate (mm)
Battery, Motor, and Powertrain | 51.244 | 866.5 | 207 | 0
Front Suspension Assembly | 10.656 | 2150 | 375 | 0
Rear Suspension Assembly | 16.712 | 550 | 550 | 0
Top Right Wheel, Tire, and Brake Assembly | 9.843 | 2150 | 206 | 625
Top Left Wheel, Tire, and Brake Assembly | 9.843 | 2150 | 206 | -625
Bottom Right Wheel, Tire, and Brake Assembly | 13.843 | 550 | 206 | 625
Bottom Left Wheel, Tire, and Brake Assembly | 13.843 | 550 | 206 | -625
Steering Assembly | 11.796 | 2000 | 415 | 0
Driver, Firewall, Harness, and Seat | 116.71 | 1400 | 425 | 0
Spaceframe and Wings | 38.972 | 1400 | 600 | 0

Refer to B.2 for the locations of the center of mass of each volume.

Page 13

Group FSAE 2 | Modelling Report

xmm =

PN
i=1 mixi
M

⇒ COMx =

381439.38mm
293.46kg | = 1299.79mm | (3.2)

ymm =

PN
i=1 miyi
M

⇒ COMy =

111434.019mm
293.46kg | = 379.72mm | (3.3)

zmm =

PN
i=1 mizi
M

⇒ COMz =

0mm
293.46kg = 0mm | (3.4)

## 3.3 Load Transfer

### 3.3.1 Longitudinal Load Transfer

The center of gravity is the location of rotation for breaking and acceleration inputs. The

vehicle will squat when accelerating and dive when braking relative to the center of gravity.

To mitigate this rotation, a counter rotation needs to be applied to the center of gravity.

This opposing rotation is induced by anti-squat and anti-dive geometry.

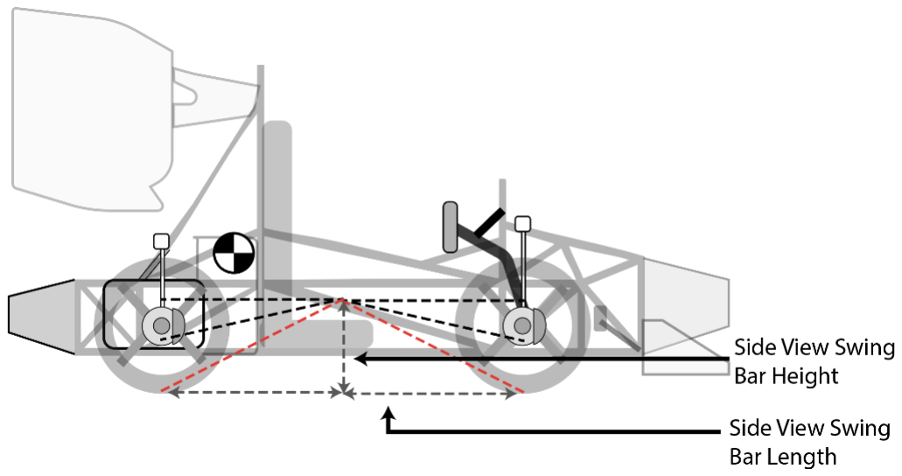
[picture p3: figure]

Figure 3.1: Anti-squat Geometry (left red line) and Anti-dive Geometry (right red line)

Anti-squat applications are added to the rear since the rear wheels squat while accel-

erating. The anti-squat geometry is determined using the swing arm length and height,

Page 14

Group FSAE 2 | Modelling Report

wheelbase, and height of the center of gravity. The rear suspension’s compression percentage can be modeled using the height of the center of gravity (h), wheelbase of the vehicle

(L), and the dimensions of the swing arm length.

% Anti Squat = tan ∅A
h/L
× 100 | (3.5)

Where,

tan ∅R =

Side View Swing Arm Height
Side View Swing Arm Length | (3.6)

Anti-dive geometry is applied for the front wheels since the front wheels experience

compression whenever the car brakes. Anti-dive geometry prevents the car from diving

onto the brakes and deflecting vertically. The percentage of front suspension’s compression can be mathematically modeled using the height of the center of gravity (h), wheelbase of

the vehicle (L) and the dimensions of the virtual side view swing arm length [4].

% Front Anti Dive = % Front Braking × tan ∅A ×

L
h

(3.7)

### 3.3.2 Lateral Load Transfer

The car experiences rotation around a virtual point being the roll centre. The roll centre

convention assumes that a load is applied on the center of the wheel. The roll center can

be located using the geometry in figure 4.13.

Page 15

Group FSAE 2 | Modelling Report

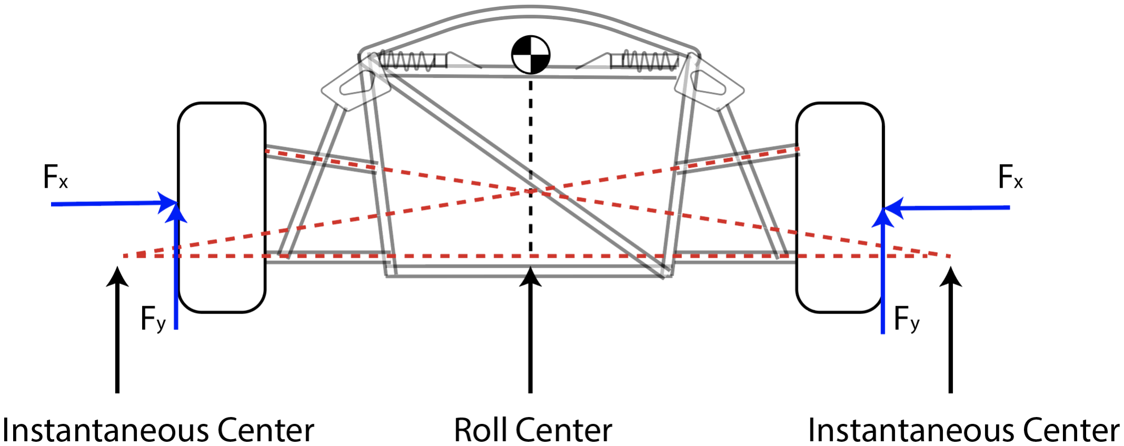
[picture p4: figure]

Figure 3.2: Suspension Geometry to Locate Instantaneous Points and Roll Centre

The instantaneous points act as a pivot where the force rotates on the imaginary red

lines, subsequently causing a rotation around the line. As the vehicle accelerates, the x

component of the force is applied on the control arms and the y component force moves the suspension around its instantaneous center [5].

## 3.4 Assumptions and Working Environment

The FSAE vehicle is assumed to operate under clear weather conditions while being sus-

ceptible to high impact crashes. The driver of the vehicle is assumed to be a 95th percentile

male with a weight of 111.58 kg. The total weight of the vehicle with the driver is cal-

culated to a total of 297 kg. The vehicle is assumed to be operating using its maximum speed and acceleration, 105 km/hr and 6 m/s²
respectively.

Page 16

# Chapter 4

# Kinematics and Applied Forces

## 4.1 2 Dimensional Kinematic Model of Vehicle

Illustrated below is a figure which represents a 2 dimensional model of a car in motion.

The parameters can be defined as:

q =

x

y

θ

(4.1)

The 4 Degrees of Freedom are represented as the vehicles position on the x-axis, y-axis and

along the vehicle’s steering angle θ

Assuming small velocities, the dynamics of the vehicle can be described using a single-track model [6]

x˙

y˙
˙θ

φ˙

=

cos(θ)

sin(θ)

1
L

∗ tan(φ)

0

v =

0

0

0

1

ω | (4.2)

Where x and y define the position of the midpoint of the rear axle, θ refers to the orientation of the car relative to the x-axis, and φ refers to the steering angle. [7]

Hence, it is determined that the motion of the car can be determined using the equations

17

Group FSAE 2 | Modelling Report

below. It can easily be demonstrated that 4.3 and 4.4 are the velocity components of the

car in the x and y coordinates, and 4.5 is the angular velocity of the vehicle.

x˙ = v cos(θ); | (4.3)
y˙ = v cos(θ); | (4.4)

˙θ =

v
L
tan(φ) | (4.5)

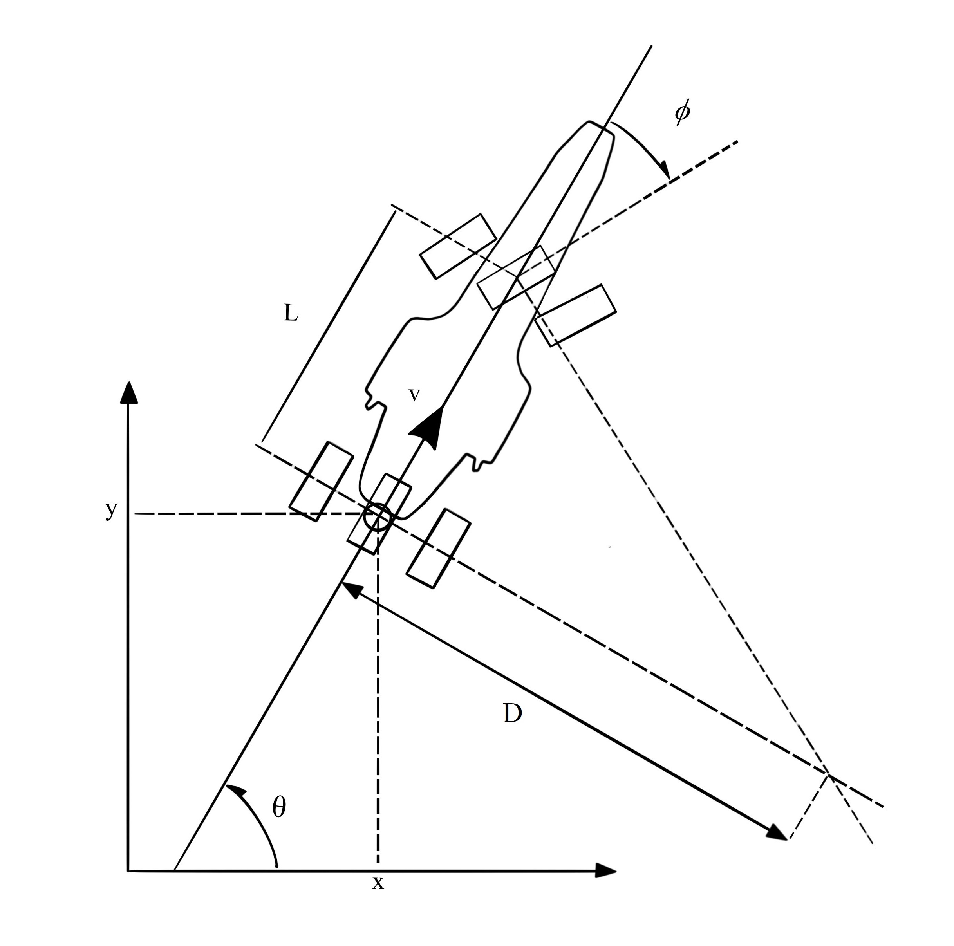
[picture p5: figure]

Figure 4.1: 2-D Kinematic Model of Vehicle

## 4.2 Steady State Low Speed Cornering Geometry and

## Vehicle Turning Radius

The figure below illustrates an Ackermann Geometry also known as a kinematic steering

geometry. The Ackermann geometry states that for a basic steering system for a front

wheel steering system, the difference of the cotangents of the angles of the outer front

Page 18

Group FSAE 2 | Modelling Report

wheels to the inner front wheels should equate to the ratio of the width (T) and length (L)

of the vehicle.

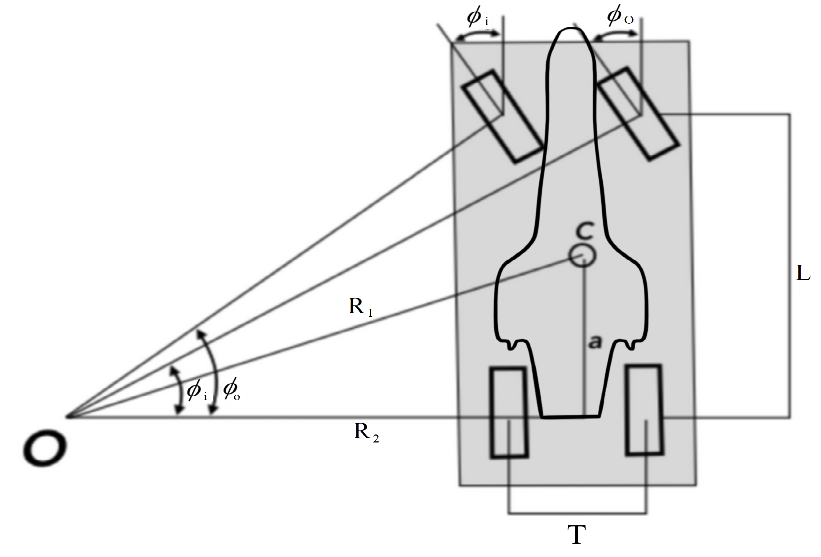
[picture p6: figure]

Figure 4.2: Vehicle Steering Ackermann Method

This condition can be simply modeled by the following set of equations:

cot(φi) − cot(φo) = T
L

(4.6)

Where, φi

is the steering angle of the inner front wheel,φo is the steering angle of the

outer front wheel, T is the vehicle’s track width, and L is the wheelbase of the vehicle.

As seen in figure 4.2 it can be seen that if a normal is drawn from all the wheels they

intersect at a point O which is the center of rotation. The vehicle’s center of mass will

turn with a radius R1. This is known as the turning radius, which can be geometrically

defined as follows:

R1 =

r
a

2 + (L²

)((cot(φo) + cot(φi)
2

)

2
(4.7)

Where, a is the distance from the rear axle to the center of mass and is 0.739 m. Assuming

R2 = 5m, and provided L = 1.65m and T = 1.11m. Then, the turning radius of the vehicle

can be determined as follows:

Page 19

Group FSAE 2 | Modelling Report

φo = arctan

L
R2 +

T
2

!
= arctan
1.65m
5m +

1.11m
2
= 0.2804rad | (4.8)

φi = arctan

L
R2 −

T
2

!
= arctan
1.65m
5m −

1.11m
2
= 0.3455rad | (4.9)

R1 =

r
(.739m)

2 + (1.65m)

2
(

(cot(.2804rad) + cot(.3455rad) 2

)

2 = 5.209m (4.10)

Hence, from the above series of equations it can be determined that the turning radius

of the center mass of the vehicle would be 5.21 meters.

## 4.3 Static Applied Forces

### 4.3.1 Forces Applied on a Car Parked on a Level Road

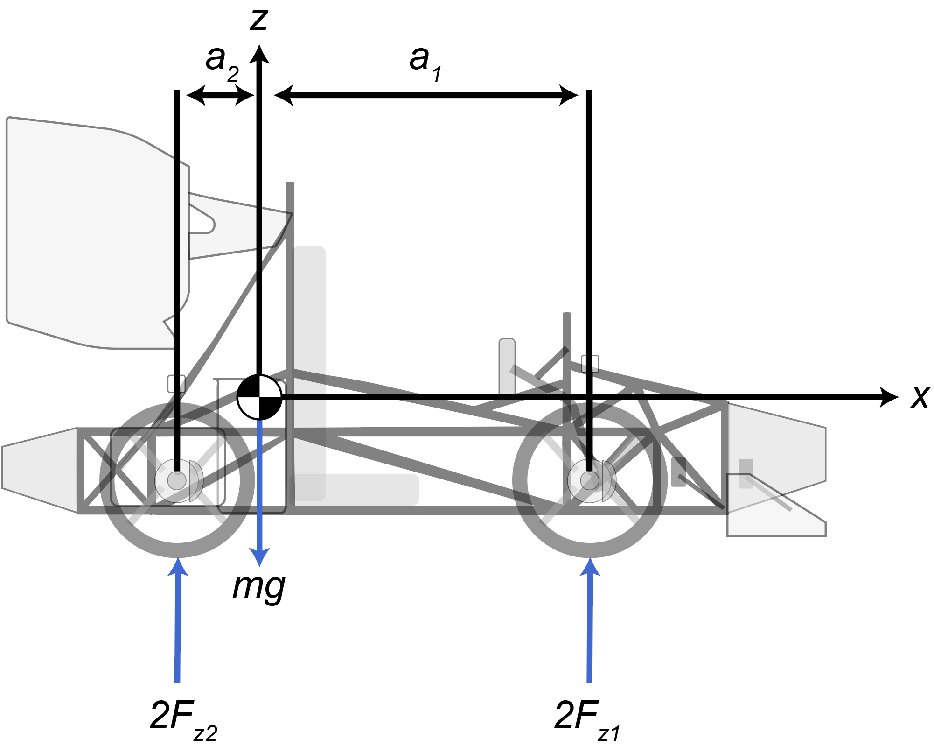
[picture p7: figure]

Figure 4.3: FBD of Car on a Level Road

Page 20

Group FSAE 2 | Modelling Report

The reaction forces on the wheels of a car parked on a level road can be found as follows:

Fz1 =

1
2

mg

a2
(a2 + a1)

=

1
2

(297kg)(9.81

m
s

2

)

(0.75m)
(0.75m + 0.9m)
= 662.1 N | (4.11)

Fz2 =

1
2

mg

a1
(a2 + a1)

=

1
2

(297kg)(9.81

m
s

2

)

(0.9m)
(0.75m + 0.9m)
= 794.6 N | (4.12)

### 4.3.2 Forces Applied on a Car Parked on an Inclined Road

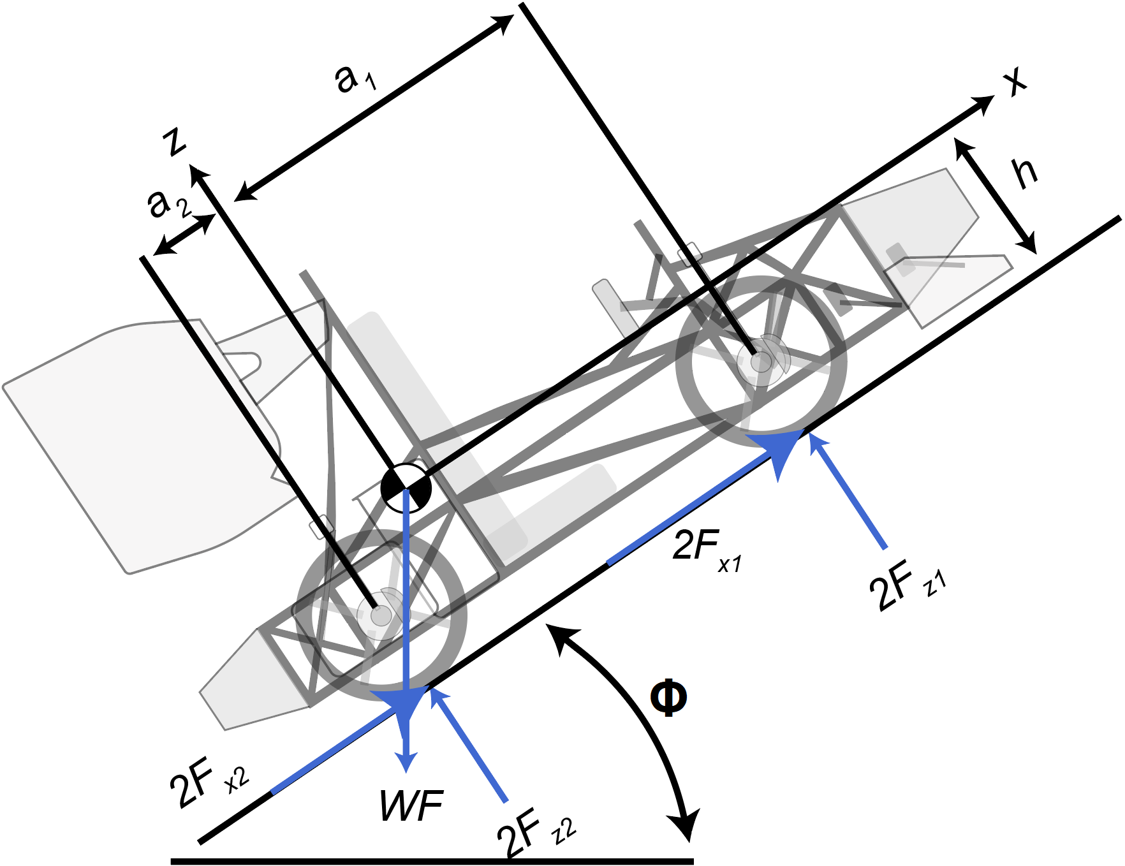
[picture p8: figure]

Figure 4.4: FBD of Car on an Inclined Road

The normal forces acting on the wheels of a car parked on an inclined road can be found

as follows:

Fz1 =

1
2

mg
a2
a2 + a1

cos φ −

h
a2 + a1

sin φ

(4.13)

Fz2 =

1
2

mg
a1
a2 + a1

cos φ +

h
a2 + a1

sin φ

(4.14)

Assuming a coefficient of static friction µs = 0.7, the friction forces at the wheels are found

to be:
Fx1 = µsFz1 = (0.7)(594.01 N) = 415.81 N | (4.15)
| Page 21

Group FSAE 2 | Modelling Report
Fx2 = µsFz2 = (0.7)(840.64 N) = 588.45 N | (4.16)

Assuming a typical angle of incline as φ = 10◦ , the reaction forces can be calculated as

follows:

Fz1 =

1
2

(297kg)(9.81

m
s

2

)( (0.75m)
(0.75m + 0.9m)

cos(10◦
) −

(0.379m)
(0.75m + 0.9m)

sin(10◦
)) = 594.01 N

(4.17)

Fz2 =

1
2

(297kg)(9.81

m
s

2

)( (0.9m)
(0.75m + 0.9m)

cos(10◦

) + (0.379m)
(0.75m + 0.9m)

sin(10◦
)) = 840.64 N

(4.18)

### 4.3.3 Forces Applied on a Car Parked on a Banked Road

When a car is parked on a banked road, the load is distributed differently between each

side of the car, with a larger load experienced by the lower tires. To illustrate this, an

FBD for the front wheels on a banked road is used, where the load experienced on the front wheels corresponds to the load on the front axle (WF ).

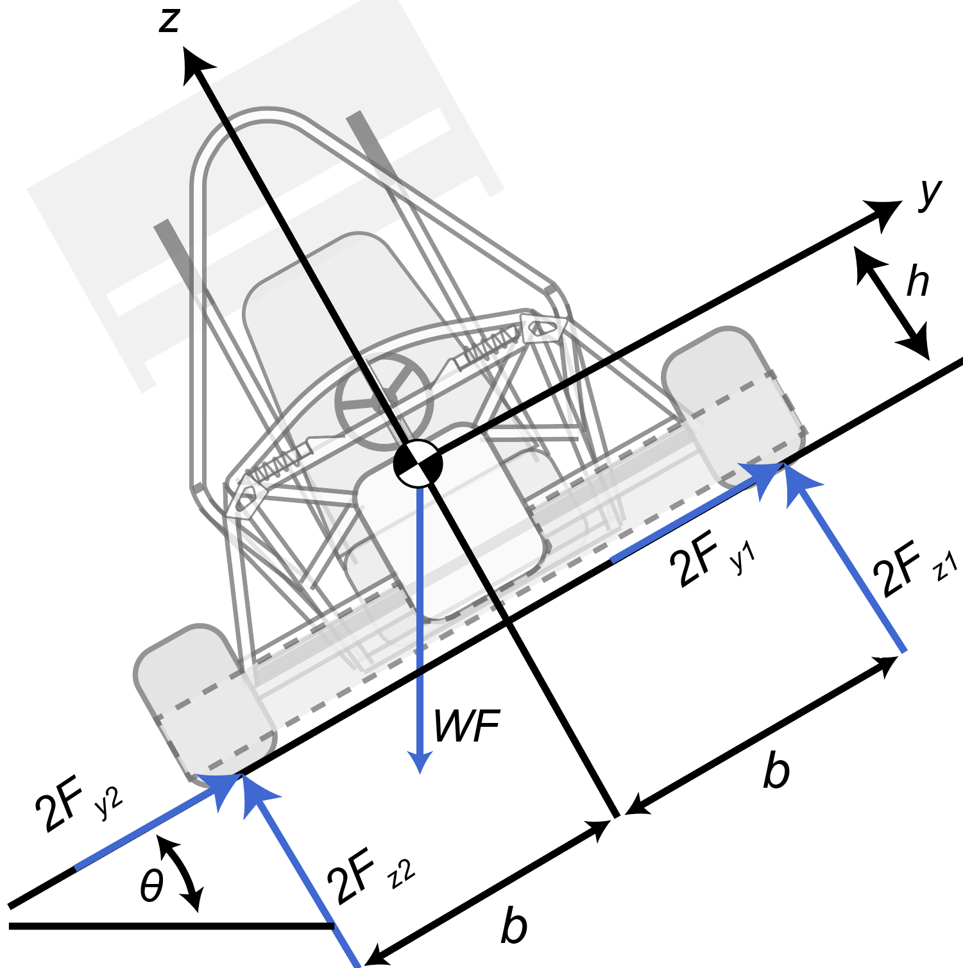
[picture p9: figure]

Figure 4.5: FBD of Car on a Banked Road

Page 22

Group FSAE 2 | Modelling Report

The reaction forces above are found as follows [8]:

Fz1 =

WF
2b
(b cos θ − h sin θ) | (4.19)

Fz2 =

WF
2b
(b cos θ + h sin θ) | (4.20)

To calculate for the normal forces experienced by the front wheels, WF is first found by

multiplying the value for Fz1

from section 4.3.1 by the cosine of the bank angle θ. Assuming the bank angle to be θ = 10◦
, thus giving WF = 652.04N.

Fz1F RONT =

652.04N
2(0.625m)

(0.625 cos(10◦

) − 0.379 sin(10◦
)) = 286.76 N | (4.21)

Fz2F RONT =

652.04N
2(0.625m)

(0.625 cos(10◦

) + 0.379 sin(10◦
)) = 355.43 N | (4.22)

Using a coefficient of friction µs = 0.7, the following friction forces can be found:

Fy1F RONT = (µs)(Fz1F RONT ) = (0.7)(286.76N) = 200.73 N | (4.23)
Fy2F RONT = (µs)(Fz2F RONT ) = (0.7)(355.43N)248.8 N | (4.24)

Similarly, calculating for the normal forces experienced by the rear wheels on a banked

surface uses the same equations as the front. However, the normal forces experienced in the rear wheels correspond to the load on the rear axle (WR) which is the value for Fz2
| from
equation (4.12) multiplied by the cosine of the bank angle. Again it is assumed θ = 10◦
| ,

thus giving WR = 782.53N.

Fz1REAR =

782.53N
2(0.625m)

(0.625 cos(10◦

) − 0.379 sin(10◦
)) = 343.93 N | (4.25)

Fz2REAR =

782.53N
2(0.625m)

(0.625 cos(10◦

) + 0.379 sin(10◦
)) = 426.28 N | (4.26)

Page 23

Group FSAE 2 | Modelling Report

Using µs = 0.7 the following friction forces can be found:

Fy1REAR = (µs)(Fz1REAR) = (0.7)(343.93N) = 240.75 N | (4.27)
Fy2REAR = (µs)(Fz2REAR) = (0.7)(426.28N) = 298.4 N | (4.28)

## 4.4 Dynamic Applied Forces

### 4.4.1 Acceleration on a Level Road

An accelerating car on a level road gives has reaction forces on the wheels as seen in the

figure below. In this situation load is transferred longitudinally shifting the load more to

the driven wheels, or rear wheels, causing the car to squat. Additionally, the friction force

is only considered for the driven wheels since the front wheels are free-rolling and thus friction on them is assumed negligible [8].

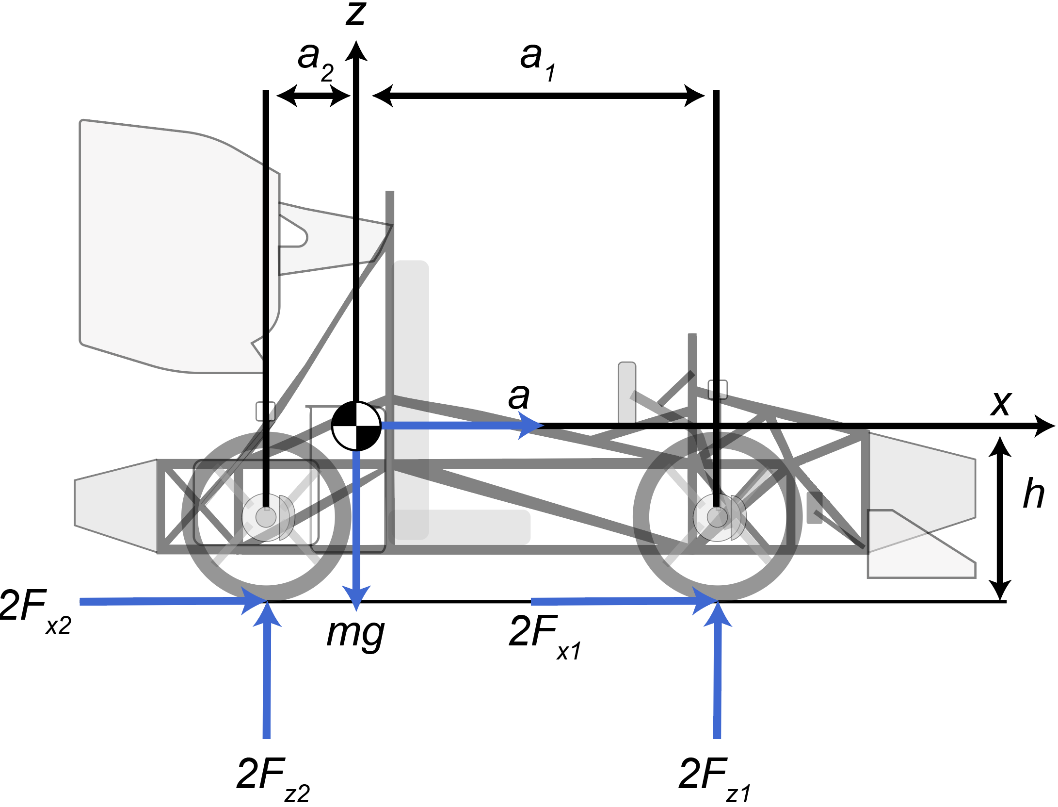
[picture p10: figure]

Figure 4.6: FBD of an Accelerating Car on a Level Road

The forces in the FBD above can be found as follows, where it is assumed µk = 0.6 [8]:

Fz1 =

1
2

(mg)(( a2
a2 + a1

) − (

h
a1 + a2

)(a
g
)) | (4.29)
| Page 24

Group FSAE 2 | Modelling Report

Fz2 =

1
2

(mg)(( a1
a2 + a1

) + ( h
a1 + a2

)(a
g
)) | (4.30)
Fx2 = µkFz2 = 0.6 × 589.95N = 353.97 N | (4.31)

Assuming an acceleration of a = 6 m
s

2

, the normal forces are calculated as:

Fz1 =

1
2

(297kg×9.81

m
s

2

)(( 0.75m
0.9m + 0.75m

)−(( 0.379m
0.9m + 0.75m

)( 6m
9.81 m
s

2

)) = 457.52 N (4.32)

Fz2 =

1
2

(297kg×9.81

m
s

2

)(( 0.9m
0.9m + 0.75m

)+(( 0.379m
0.9m + 0.75m

)( 6m
9.81 m
s

2

)) = 589.95 N (4.33)

### 4.4.2 Acceleration on an Inclined Road

Below is a depiction of the applied forces on a car while accelerating on an incline. The

principle stays the same as acceleration on a level road, however the extent of load transfer

and thus magnitude of each reaction force is changed due to the additional acceleration induced by gravity [8].

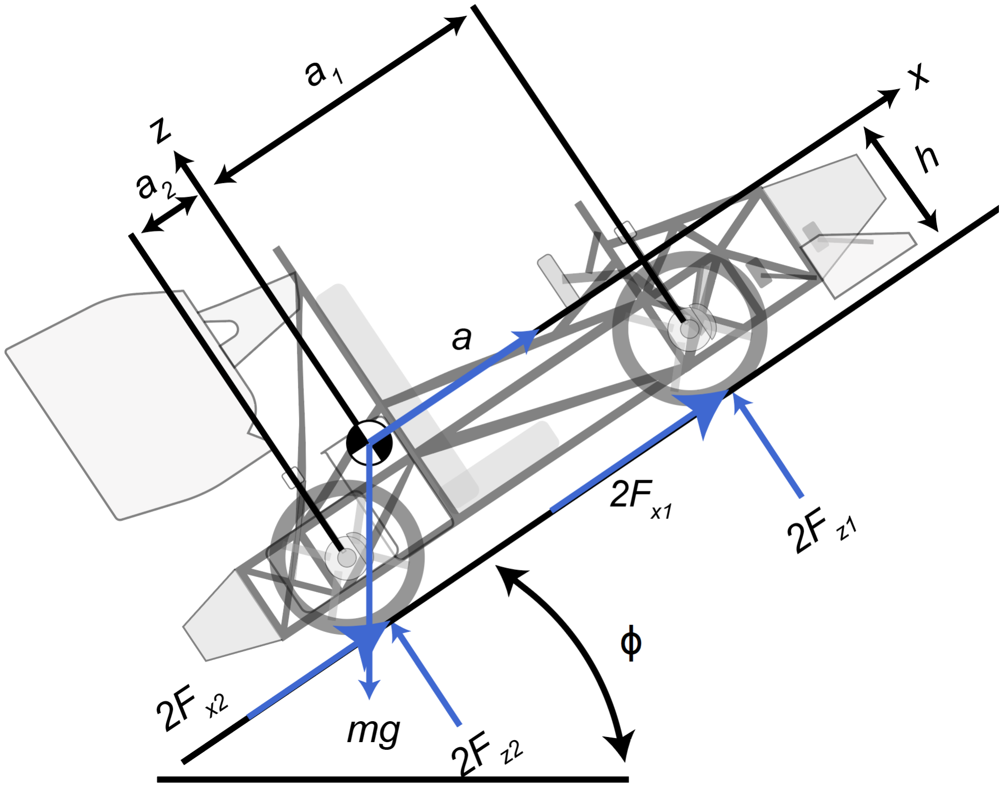
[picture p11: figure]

Figure 4.7: FBD of an Accelerating Car on an Inclined Road

Fz1 =

1
2

mg
a2
a1 + a2

cos φ −

h
a1 + a2

sin φ

−

1
2

(ma)

h
a1 + a2

(4.34)

Page 25

Group FSAE 2 | Modelling Report

Fz2 =

1
2

mg
a1
a1 + a2

cos φ +

h
a1 + a2

sin φ

+

1
2

(ma)

h
a1 + a2
= | (4.35)

Assuming a typical angle of incline as φ = 10◦ and a typical acceleration as a = 6 m
| s
| 2 ,

the values for Fz can be calculated as:

Fz1 = 389.35 N | (4.36)
Fz2 = 1045.30 N | (4.37)

Assuming a coefficient of kinetic friction µk = 0.6, the friction force on the rear wheels is:

Fx2 == µkFz2 = 0.6 × 1045.3N = 627.18 N | (4.38)

### 4.4.3 High Speed Cornering

During a turn at a relatively high velocity, a centripetal force is produced which transfers

the load laterally to the side of the car inside a turn. For a car moving at a reasonable

velocity v, around a corner with a radius of curvature R, there is an applied centripetal force (F c).With the assumption that v = 15m
s

and that the radius of curvature is R = 30m,

the centripetal force can be calculated as follows below. It should be noted that this radius of curvature is close to the maximum value of R that is allowed in the FSAE guidelines [9].

FC =

mv²
R

= (297 kg)

(15 m
s

)

2
30 m
= 2227.5 N | (4.39)

A consequence of FC when turning, is that the load is transferred laterally from one side

of the car to the other. That is, more load is placed on the wheels on the inside of a turn,

causing the car to roll. To illustrate this, an FBD for the front wheels during a corner is

used, where the load experienced on the front wheels corresponds to the load on the front axle (WF ). The value for WF is equal to the value from section 4.3.1 found in section

section 4.3.1.

| Page 26

Group FSAE 2 | Modelling Report

Figure 4.8: Reaction at Wheels Due to Applied Centripetal Force

The reaction forces above are found as follows:

Fz1F RONT =

bWF − hFC
2b
= −344.3 N | (4.40)

Fz2F RONT =

bWF + hFC
2b
= 1006.46 N | (4.41)

Assuming a kinetic friction coefficient µk = 0.6, its found:

Fy1F RONT = (µs)(Fz1F RONT ) = (0.6)(−344.3N) = −206.58 N | (4.42)
Fy2F RONT = (µs)(Fz2F RONT ) = (0.6)(1006.46N) = 603.88 N | (4.43)

Similarly, calculating for the normal forces experienced by the rear wheels during a

turn uses the same equations as the front. However, the normal forces experienced in the rear wheels correspond to the load on the rear axle (WR) which is equal to the value for

Fz2

from equation (4.12).

Fz1REAR =

bWR − hFC
2b
= −278.07 N | (4.44)
| Page 27

Group FSAE 2 | Modelling Report

Fz2REAR =

bWR + hFC
2b
= 1027.68 N | (4.45)

Assuming a kinetic friction coefficient µk = 0.6, friction forces can be found:

Fy1REAR = (µs)(Fz1REAR) = (0.6)(−278.07N) = −166.84 N | (4.46)
Fy2REAR = (µs)(Fz2REAR) = (0.6)(1027.68N) = 643.61 N | (4.47)

### 4.4.4 Braking

As per the Formula SAE rules and regulations, the brake pedal must be designed to

withstand a force of 2000N without any failure of the brake system or pedal box. In this

analysis, it is assumed that all parts are perfectly rigid, fluids are incompressible, and heat

loss is minimal. By summing the moments about the pivot tube shown below, the force output can be found [10].

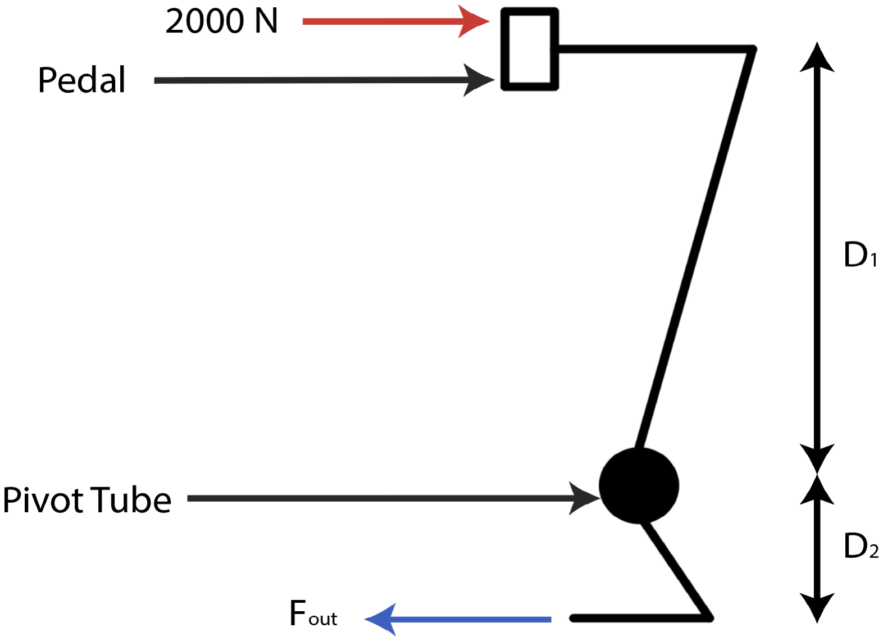
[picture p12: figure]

Figure 4.9: FBD of the maximum force exerted by the driver on the brake pedal

0 = Mout + Min | (4.48)
Fout D2 = −Fin D1 | (4.49)

Page 28

Group FSAE 2 | Modelling Report

Fout = −2000N

0.2m
0.05m
= −8000N | (4.50)

A balance bar divides the force from the brake pedal to the two master cylinders. The

torque on one side of the bar must balance the torque on the other side of the bar. By

summing the moments, the force going into the master cylinders can be determined.

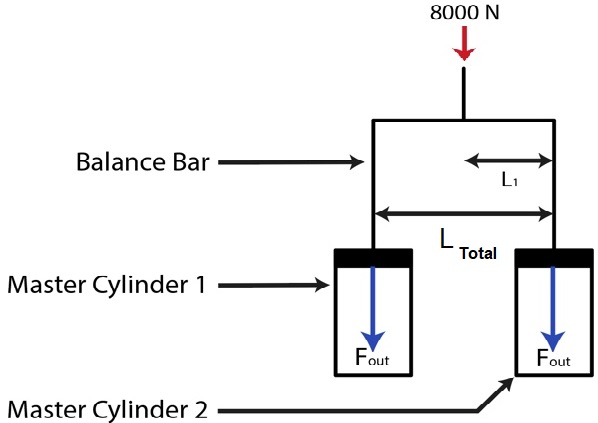
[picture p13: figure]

Figure 4.10: FBD of the balance bar and the two master brake cylinders

Fout Ltotal = Fin L1 | (4.51)

Fout = 8000 N
0.05 m

0.1 m
= 4000 N | (4.52)

Each master cylinder is connected to two calipers. Using Pascal’s Law, a relation is de-

veloped depending on the master cylinder bore size and the caliper’s piston diameter to

solve for the force acting on a single rotor. The master cylinder bore size was assumed to

be 20mm and the diameter of the piston was assumed to be 40mm.

Page 29

Group FSAE 2 | Modelling Report

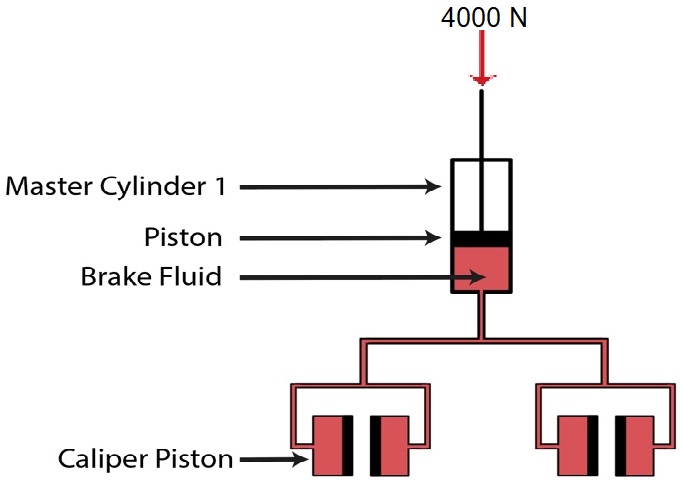
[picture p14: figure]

Figure 4.11: FBD of one master cylinder and the two calipers

For each individual caliper with two pistons, the total force at both pistons is:

Fcal = 2Fcyl
Acal

Acyl
= 2(4000N)
π(0.02m)

2
π(0.01m)

2

= 32000 N | (4.53)

The caliper’s pistons are pushed against the brake pads, where the actual braking force

can be determined depending on the brake pads coefficient of friction. In this calculation,

the brake pad coefficient of friction is assumed to be 0.45.

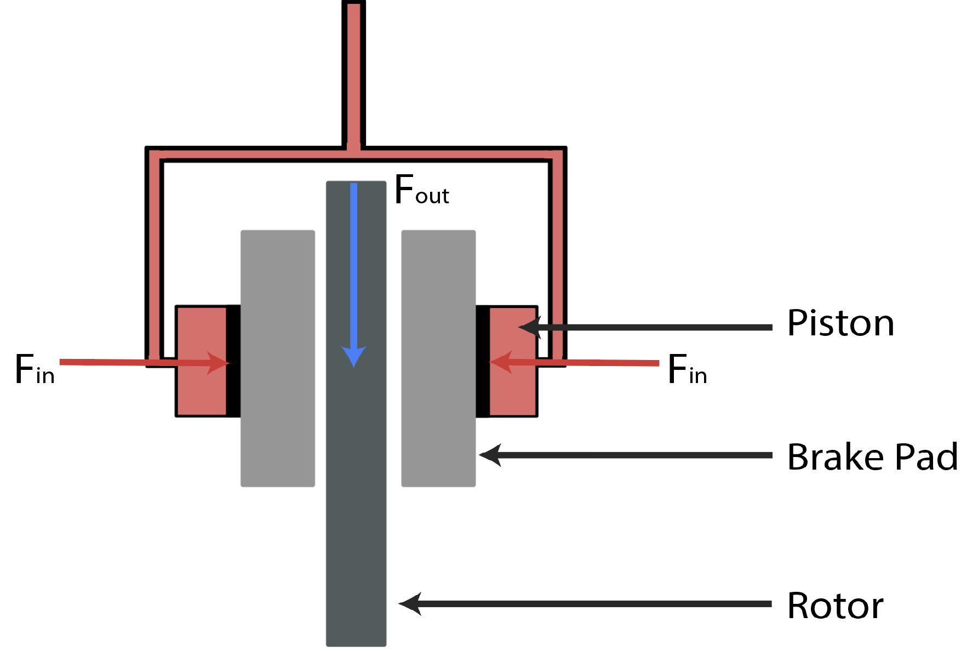
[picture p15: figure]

Figure 4.12: FBD of the caliper and rotor

Fout = µFin = 0.45(32000 N) = 14400 N | (4.54)
| Page 30

Group FSAE 2 | Modelling Report

The braking force is dependent on the radius of the rotor and wheel. A larger rotor

radius will increase the brake torque produced by the brake system. It is assumed that the wheel has a radius (R) of 206mm and the rotor has a radius (r) of 124mm.

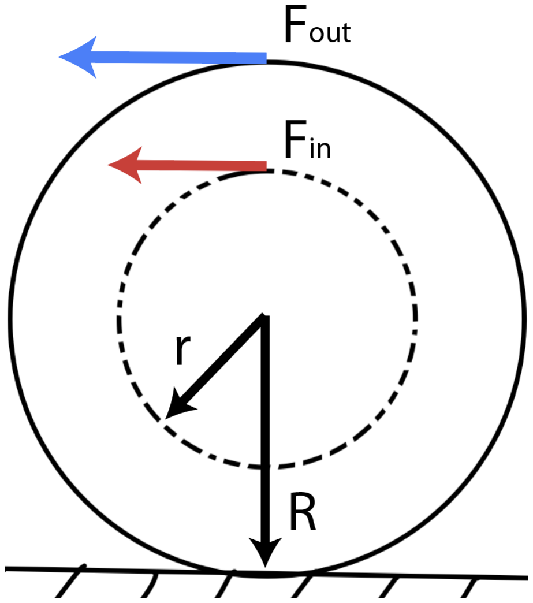
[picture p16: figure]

Figure 4.13: FBD of the wheel on the road

Fout = Fin r
R

= 14400 N
124 mm

206 mm
= 8668 N | (4.55)

A braking force of 8668N is exerted on each wheel for a total braking force of 34672N on

the vehicle. The analysis shows that a decrease in master cylinder size, increase in caliper

piston area, or increase in the pedal ratio will ultimately increase the braking force on the wheels [11].

### 4.4.5 Impacts and Collisions

As per FSAE rules and regulations, the impact attenuator must decelerate the vehicle at

a rate not exceeding 20g average. The energy absorbed must meet or exceed 7350J when the total mass of the vehicle is 300kg at an impact velocity of 7.0m/s [12].

aavg = 20
9.81 m/s

2
= 196.2 m/s

2
(4.56)

Solving for kinetic energy yields:

Page 31

Group FSAE 2 | Modelling Report

Ke =

1
2

mv²
impact =

1
2
(300 kg)(7 m/s)² = 7350 J | (4.57)

By conservation of energy, kinetic energy is equal to potential energy.

Ke = Pe | (4.58)

Solving for time of impact at a deceleration of 20g yields:

t =

vimpact

aavg

=

7 m/s
196.2 m/s

2

= 0.036 s | (4.59)

Solving for impulse as the vehicle comes to a full stop from 7m/s yields:

Im = m (vimpact − vfinal ) = 300 kg(7 m/s − 0m/s) = 2100 N · s | (4.60)

Lastly, the impact force that the impact attenuator will be subjected to at 20g is:

F =

Im
t

=

2100 N · s
0.036 s
= 58, 333 N | (4.61)

### 4.4.6 Slip Angle

The slip angle of a vehicle describes the ratio of transverse and radial velocities in the

form of an angle. It is the angle in between the wheel actual direction of motion and the direction that it is pointing towards [13].

Page 32

Group FSAE 2 | Modelling Report

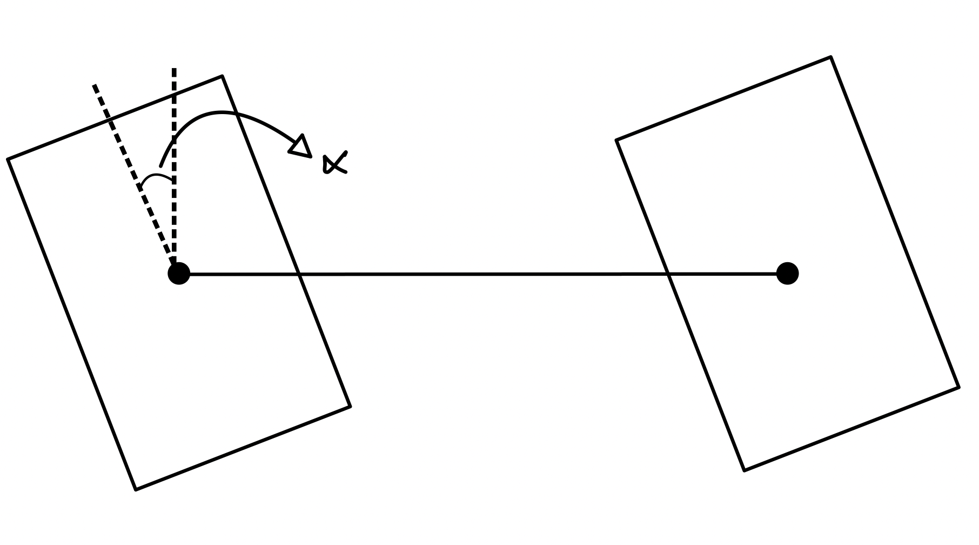
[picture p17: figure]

Figure 4.14: Slip Angle Representation

The slip angle is dependant on the load on the tire which differs from the rear and front tires. The slip angle can be mathematically modeled as the following equation [14].

α =

W · v

2
Cα · g · R

(4.62)

Where W is the load on the tire, v is the velocity of the tire, C is the tire stiffness coefficient which will be assumed to be 867 N/◦
[15], g is gravity, and R is the turning

radius of the center of mass.

αfr =

330.8N · 29.2

2m/s
867N/◦
- 9.8m/s²
- 5.21m

= 6.37◦
(4.63)

αre =

396.9N · 29.2

2m/s
867N/◦
- 9.8m/s²
- 5.21m

= 7.64◦
(4.64)

### 4.4.7 Aerodynamics

### 4.4.7.1 Aerodynamic Effects at Max Speed

To analyse the aerodynamics effects of the vehicle appropriately, a model needs to be

created for when the vehicle is at its top speed which represents the highest aerodynamic

Page 33

Group FSAE 2 | Modelling Report

forces acting on the vehicle at any given point in time. A car’s acceleration can be modeled

according to newton’s second law as:

mx¨ = F −

1
2

ρCDAx˙

2
(4.65)

where F is the force propelling the vehicle forward, ρ is the density of air, CD is the drag

coefficient, and A is the frontal area of the vehicle. The driving force F can be expressed in

terms of motor power and the car velocity where v = ˙x . This, can be simplified to when the vehicle is in equilibrium and is not accelerating to become [?]:

P =

CDAv³
1.633

(4.66)

Now provided the motor used to estimate our battery calculations can produce a max-

imum of 100 kW peak power, and assuming transmission losses. Then the power at the

wheels is assumed to be 84 kW. Moreover, assuming a drag coefficient CD = 0.63 for a car with no aerodynamic packages, [16] and a frontal area of A = 1.34m²
. Then solving

for the max speed of the vehicle one can find that the max velocity which the motor can

produce to the tires is:

v =

3

r
1.633P
CDA

=

3

r
1.633 × 84000KW
.63 × 1.34m²

= 54.56m/s = 196.4km/hr (4.67)

To determine the maximum drag coefficient desired whilst the vehicle is competing in its endurance races, a maximum top speed of 105km/hr can be assumed. Solving for the

coefficient of drag:

CD =

1.633P
Av³ ⇒ CD =

1.633 × 84000KW
1.34m² × (29.17m/s)
3 ⇒ CD = 4.125 | (4.68)

Thus, the maximum allowable coefficient of drag is therefore 2.85. Which is a very high

coefficient of drag, which indicates that the drag induced would not limit the top speed of

Page 34

Group FSAE 2 | Modelling Report

the vehicle beyond its intended purpose.

### 4.4.7.2 Aerodynamic Effects on Cornering Performance

This section will analyse the aerodynamic effects induced on the tyres whilst cornering.

This can be demonstrated by analysing the maximum allowed velocity a vehicle can corner

at without losing its grip. Which is the velocity at which the fictional force is equal to the centripetal force [17].

µFz = µ(mg +

1
2

ρCLAv²

) = mv²
R

(4.69)

v =

r µmg

m
R −
1/2 ρCLAµ | (4.70)

Where, g is the gravitational acceleration, µ is the coefficient of friction, ρ is the air

density, CL is the coefficient of lift, A is the frontal area, and R is the radius of the

corner. According to the FSAE rules the corners will vary in radii from 4.5 to 30 m

for dynamic events. Thus, assuming a lift coefficient when no aerodynamic packages are

installed is CL = 0.29, and the lift coefficient when aerodynamic packages are installed is CL = 2.34 [16], and the density of air to be ρ = 1.225, assuming a constant coefficient of friction of µ = 0.65, and provided the mass of the car is 298 kg, the frontal area A = 1.34m² ,
then the following can be calculated from a 9-30 m turn radius [9]:

Table 4.1 illustrates the different speeds which can be achieved as the vehicle is cornering

with an aerodynamic package installed, and without one. Clearly, higher speeds can be

achieved whilst cornering when an aerodynamic package is installed, as there is more down-

force acting on the vehicle.

Page 35

Group FSAE 2 | Modelling Report

Table 4.1: Cornering Speed differences with and without an Aerodynamic Package

Corner RadiusR (m) | With Aerodynamic Package | W/O Aerodynamic Package
| Velocity (km/hr) | Velocity (km/hr)
4.5 | 19.42 | 19.30
8 | 26.04 | 25.75
12 | 32.10 | 31.56
16 | 37.31 | 36.48
20 | 41.99 | 40.81
24 | 46.31 | 44.74
28 | 50.36 | 48.37
30 | 52.30 | 50.08

### 4.4.7.3 Load Distribution Model

This section serves the purpose of illustrating how different forces and moments act on the

vehicle. It will also introduce how the reaction forces for the rear wheels can be calculated.

The sum of forces and moments for the diagram illustrated in figure 4.15 are illustrated below [17]:

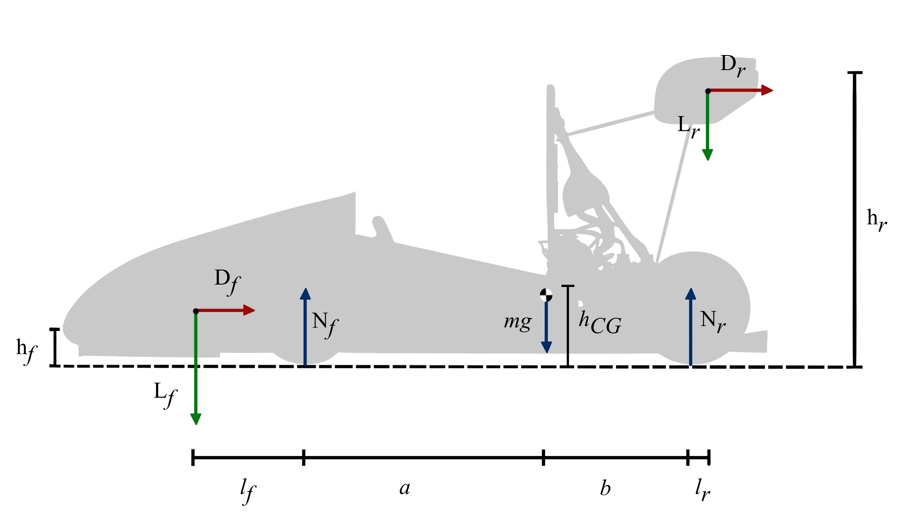
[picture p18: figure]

Figure 4.15: FBD for forces acting on the vehicle

Page 36

Group FSAE 2 | Modelling Report
ΣF = 0 ⇒ Nf + Nr − mg − LF − Lr | (4.71)

ΣMCG = 0 ⇒ bNr + (a+lf )LF −(a)Nf −(b+lr)Lr −(hCG −hr)Dr + (hCG −hf )Df (4.72)

The following can be determined after simplifying the equations of motion above:

Nr =

(lr + b) Lr − (lf + a) Lf + (hCG − hr) Dr − (hCG − hf ) Df + amg + aLf + aLr
a + b
| (4.73)

This equation gives the force on the rear tyres, which can be used to determine the load

distribution of aerodynamic forces. The forces experienced on the rear tyres of the vehicle

are therefore:

Nr = −0.363Lf + 1.1303Lr + 1493.825 + 229.455Dr − 230.051Df | (4.74)

### 4.4.7.4 Lift Forces

The lift forces on the vehicle can easily be calculated. Assuming a lift force of -2.34 [16]

with an aerodynamic package installed, and 0.29 [16] when no aerodynamic package is

installed. Then, the lift force would be:

FL1 = 0.29 × 1.34m² × 1.225kg/m² ×

(29.16m/s)

2
2
= 202.38N | (4.75)

With an aerodynamic package, the lift force acts as a down-force.

FL2 = −2.34 × 1.34m² × 1.225kg/m² ×

(29.16m/s)

2
2
= −1633.05(N) | (4.76)

Force required to lift car off the ground.

F = 298kg × 9.81m/s² = 2923.8N | (4.77)

Page 37

# References

[1] University of delaware formula SAE lincoln, car #67 2017, cost report. pages 5–8.
[2] Sony vtc6 battery specifications. https://cdn.shopify.com/s/files/1/0481/

9678/0183/files/sony_vtc6_data_sheet.pdf?v=1605015770. (https://cdn.shopify.com/s/files/1/0481/9678/0183/files/sony_vtc6_data_sheet.pdf?v=1605015770)

[3] Dr Steven Timmins. Meeg 402-010 chassis design report 2017 fsae senior design.

page 79.

[4] Anti squat, | dive and lift geometry – geometry explained. | https://

suspensionsecrets.co.uk/anti-squat-dive-and-lift-geometry/.

[5] Jonathan Vogel. Tech explained: Roll centre. https://www.racecar-engineering.

com/tech-explained/tech-explained-roll-centre/. (https://www.racecar-engineering.com/tech-explained/tech-explained-roll-centre/) Section: Tech Explained.

[6] Bernhard Muller, Joachim Deutscher, and Stefan Grodde. Continuous curvature tra-

jectory design and feedforward control for parking a car. IEEE Transactions on Control Systems Technology, 15(3):541–553, 2007.

[7] William F Milliken, Douglas L Milliken, et al. Racecarvehicledynamics, volume 400.

Society of Automotive Engineers Warrendale, PA, 1995.

[8] Forward Vehicle Dynamics, pages 39–94. Springer International Publishing AG, 3

edition.

[9] Formula SAE rules 2022.
[10] Nicholas D Galbincea. Design of the university of akron’s 2015 FSAE electric vehicle

braking system.

38

Group FSAE 2 | Modelling Report
[11] Steven Holl. | FSAE braking system: | Preliminary kinetics and dynamic
analysis. | url={https://engineerforbeer.wordpress.com/2013/10/09/

fsae-braking-system-preliminary-kinetics-and-dynamic-analysis-2/}.

[12] Craig Louis Kennedy, Jonathan Richard Hart, Justin Reed Pollard, and Todd M

LeClerc. WPI FSAE racecar crash protection.

[13] Formula1 dictionary: Slip angle. http://www.formula1-dictionary.net/slip_

angle.html. (http://www.formula1-dictionary.net/slip_angle.html)

[14] Earnest Getman. | Power steering presentation. | https://www.slideserve.com/

earnest/power-steering. (https://www.slideserve.com/earnest/power-steering)

[15] Vorotovic Goran. Determination of cornering stiffness through integration of a math-

ematical model and real vehicle exploitation parameters. 2013.

[16] Ioannis Oxyzoglou. Design & development of an aerodynamic package for a fsae race

car. University of Thessaly, 2017.

[17] Henrik Dahlberg. Aerodynamic development of formula student race car, 2014.
[18] Francesco Leotta. Design of a battery pack for a Formula SAE racing car. PhD thesis,

Politecnico di Torino, 2020.

[19] Ujjwal Ashish, Bishav Raj, and Abhishek Kumar. Design and fabrication of an accu-

mulator container/battery pack for a formula student vehicle, 2016.

Page 39

# APPENDICES

40

# Appendix A

# Data Sheets

## A.1 Sony VTC 6 Data Sheet summary

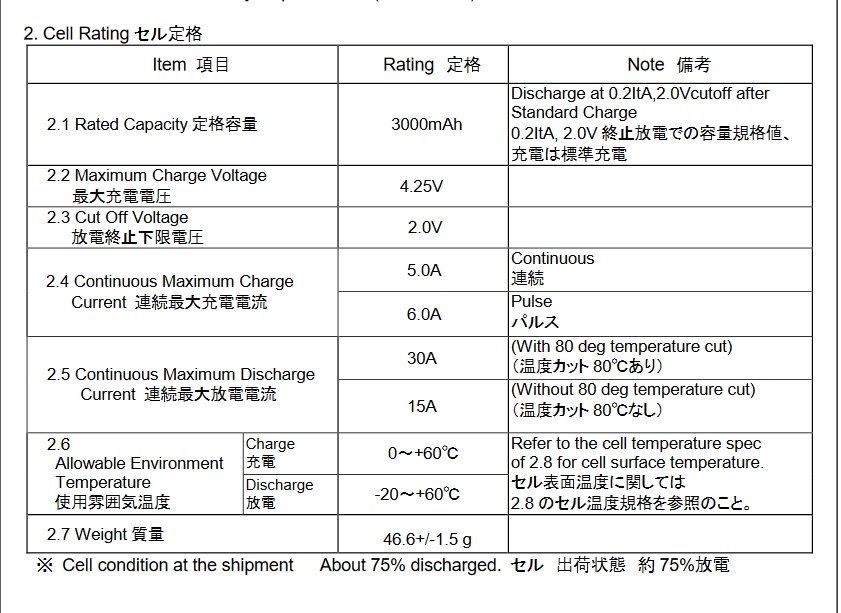
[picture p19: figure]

Figure A.1: Data Sheet for Sony VTC6 Battery Cell (1)

41

Group FSAE 2 | Modelling Report

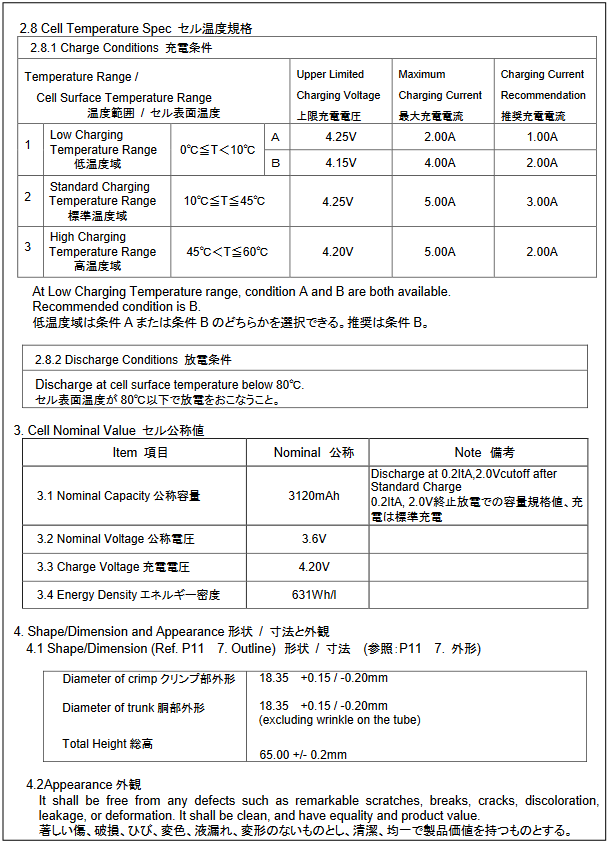
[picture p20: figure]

Figure A.2: Data Sheet for Sony VTC6 Battery Cell (2)

Page 42

Group FSAE 2 | Modelling Report
A.2 | Emrax 228 Data Sheet Summary

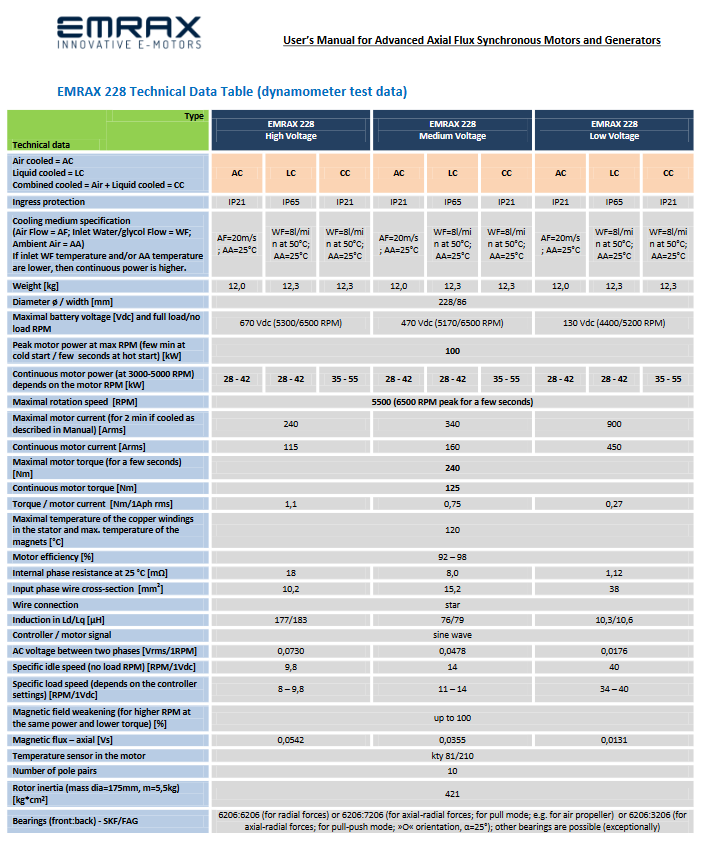
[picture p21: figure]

Figure A.3: Data Sheet for Emrax 228 Motor

Page 43

# Appendix B

# Additional material

## B.1 Accumulator Calculations

This section illustrates all the calculations used to model the battery and to estimate its

parameters.

The battery can be designed accordingly provided the following FSAE restrictions for

the accumulator.

Table B.1: FSAE Accumulator Restrictions and Guidelines

Accumulator Design Restrictions and Guidelines

EV.4.1.1 | “The maximum power drawn from the accumulator must not exceed 80 kW”
EV.4.1.2 | “The maximum permitted voltage that may occur between any two points must not exceed 600 V DC”
EV.6.1.2 | “Maximum static voltage of less than 120 V DC” “Maximum energy of 6 MJ”
F.10.3.4 | Cells and Segments “The cells and/or segments must be appropriately secured against moving inside the Container” “This mounting system design must withstand the following accelerations: 40 g in the longitudinal direction (forward/aft) 40 g in the lateral direction (left/right) 20 g in the vertical direction (up/down)”

Firstly, assuming that the Voltage that the motor will require is 500 Vdc. Indicates that

the required voltage should be within this range. Secondly, from previous FSAE electric vehicle designs [18] [18] [19] the required battery capacity can be assumed to be 6kWh.

44

Group FSAE 2 | Modelling Report

Given these starting parameters the number of required cells can be calculated , as well

as the amount of Ah needed. Therefore, for a 500 Vdc battery 12 Ah ’s are required to

have a 6kWh battery.
6000 (W h)
500 (V )
= 12 (Ah) | (B.1)

Next, the cell configuration must be determined.

Provided the nominal voltage of a single cell is 3.6 V and 3 Ah, as seen in table 2.3.

The number of cells to be connected in series that will provide 500 Vdc would be the

voltage required divided by the voltage produced by a single cell; and the number of cells

to be connected in parallel to provide the required capacity would be the capacity required

divided by the capacity of a single cell.

500 (V )
3.6 (V )
= 139 (cells) | (B.2)

12 (Ah)
3 (Ah)
= 4 (cells) | (B.3)

For the sake of design consistency, 140 cells will be connected in series rather than the

139 cells. Each cell will have to be connected to 4 cells in parallel to achieve the required

battery capacity of 6 kWh.

Hence, the total number of cells required for the battery is:

140 ∗ 4 = 560 (cells) | (B.4)

Each cell section configurations will now be modelled according to the FSAE restrictions

which state: ”A Maximum energy of 6 MJ per section” and ”No more than 12 kg per

section”

6 MJ = 1666 W h. | (B.5)
| Page 45

Group FSAE 2 | Modelling Report

Assuming, the battery is divided into 5 sections and each section is connected in series,

to produce the 504 V required. It can be determined that each section will have 28 cells

connected in series.

504 (V )
3.6 (V )
= 28 (cells) | (B.6)
28 ∗ 4 = 112 (cells) | (B.7)

Therefore, each section has 112 cells. To verify that each section satisfies the 6 MJ

energy constriction, the peak voltage and peak current discharge of the cells are taken and

multiplied to find the energy produced per section.

4.2 (V ) ∗ 28 (cells) ∗ 3 (Ah) ∗ 4 (cells) = 1411.2 (W h) ≤ 1666.7 (W h) (B.8)

To prove that the weight restrictions per section is achieved, the total number of cells per section/section can be multiplied by the mass of a single cell from 2.3.

112 (cells) ∗ .048 (kg) = 5.376 (kg) | (B.9)

Finally, given the restriction: “The maximum power drawn from the accumulator must

not exceed 80 kW” can be verified using the values obtained from the cell specification

sheet from table 2.3. Each cell has a peak voltage of 4.2 V, and peak current 30 A.

Thus,

140 ∗ 4.2 (V ) ∗ 30 ∗ 4 (A) = 70.56 (kW) ≤ 80 (kW) | (B.10)

Therefore, with all the electrical restrictions cleared, this battery model can be utilized

as a sample for our design with its final properties illustrated in table 2.4

| Page 46

Group FSAE 2 | Modelling Report
B.2 | Center of Mass Calculations

COM x-coordinate =

(51.2kg × 866.5mm) + (10.7kg × 2150mm)

+ (16.7kg × 550mm) + (9.8kg × 2150mm)

+ (9.8kg × 2150mm) + (13.8kg × 550mm)

+ (13.8kg × 550mm) + (11.8kg × 2000mm)

+ (116.71kg × 1450mm) + (39kg × 1400mm)

293.5kg

= 1299.7mm

(B.11)

COM y-coordinate =

(51.2kg × 207mm) + (10.7kg × 375mm)

+ (16.7kg × 550mm) + (9.8kg × 206mm)

+ (9.8kg × 206mm) + (13.8kg × 206mm)

+ (13.8kg × 206mm) + (11.8kg × 415mm)

+ (116.71kg × 425mm) + (39kg × 600mm)

293.5kg

= 379.7mm (B.12)

COM z-coordinate =

(51.2kg × 0mm) + (10.7kg × 0mm)

+ (16.7kg × 0mm) + (9.8kg × 625mm)

+ (9.8kg × −625mm) + (13.8kg × 625mm)

+ (13.8kg × −625mm) + (11.8kg × 0mm)

+ (116.71kg × 0mm) + (39kg × 0mm)

293.5kg

= 0mm (B.13)

Page 47

Group FSAE 2 | Modelling Report
B.3 | Nomenclature

Table B.2: Nomenclature for Sections 4.1 and 4.2

Section 4.1 & 4.2

Variable | Definition
x | Position of the vehicle along the x-axis
y | Position of the vehicle along the y-axis
θ | Orientation of the car relative to x-axis
φ | Steering Angle
x˙ | Velocity component along the x-axis
y˙ | Velocity component along the y-axis
˙θ | Angular velocity of the vehicle
v | Velocity of the vehicle
C | Center of Mass
R1 | Turning radius for the center of mass
φi | Inner Steering Angle of front wheel
φo | Outer Steering Angle of front wheel
T | Vehicle’s track width
L | Vehicle’s wheel base
a | Distance from rear axle to C of M

Page 48

Group FSAE 2 | Modelling Report

Table B.3: Nomenclature for Aerodynamic Section

Section 4.5

Variable | Definition
ρ | Density of Air
CD | Coefficient of Drag
CL | Coefficient of Lift
A | Frontal Area
v | Velocity of Vehicle
x¨ | Acceleration along the x direction
F | Propulsion force of the Vehicle
µ | Coefficient of Friction
m | Mass of the Vehicle
R | Corner Radius
g | Gravitational Acceleration
Nf | Normal Force on front tyres
Nr | Normal Force on rear tyres
FL | Lift Force
Df | Drag force acting on front
Dr | Drag force acting on rear
lf | Distance from front axle to front wing
lr | Distance from rear axle to rear wing
a | Distance from center of gravity to front axle
b | Distance from center of gravity to rear axle
hf | Height from ground to front wing
hr | Height from ground to rear wing
hCG | Height from ground to center of gravity

Page 49

Group FSAE 2 | Modelling Report

Table B.4: Nomenclature for Applied, Static and Dynamic Force Sections

Symbols for Sections 4.3, 4.4.1, 4.4.2, and 4.4.3

m | Mass
g | Gravity
a | Acceleration
a1 | Distance in the x-direction from the car’s center of mass to the front axle
a2 | Distance in the x-direction from the car’s center of mass to the rear axle
b | Distance in the y-direction from the car’s center of mass to the middle of a wheel on the side of an axle
h | Distance in the z-direction from the car’s center of mass to the surface of the road
θ | Bank angle of the road from the horizontal
φ | Angle of inclination of the road from the horizontal
WF | Weight acting on the front axle
WR | Weight acting on the rear axle
µs | Coefficient of static friction
µk | Coefficient of kinematic friction
FC | Centripetal Force
v | Velocity
R | Radius of curvature of road

Page 50

Group FSAE 2 | Modelling Report

Table B.5: Nomenclature for Slip Angles

Nomenclature for Slip Angles

α | Slip Angle
Cα | Tire Stiffness
g | Gravitational acceleration
R | Turning Radius of the C of M of the vehicle
v | Velocity
Wr | Force acting on the axles front and rear

Table B.6: Nomenclature for Braking

4.4.4 braking

Min | Input moment
Mout | Output moment
Fin | Input force
Fout | Output force
D1 | Distance from pivot tube to brake pedal
D2 | Distance from pivot tube to balance bar
L1 | Horizontal distance from master cylinder piston to the center of the balance bar
LT otal | horizontal distance between the two master cylinder pistons
Fcal | Force exerted on both caliper pistons
Fcyl | Force exerted on master cylinder
Acal | Area of caliper piston
Acyl | Area of master cylinder piston
µ | Coefficient of friction
r | Radius of rotor
R | Radius of wheel

Page 51

Group FSAE 2 | Modelling Report

Table B.7: Nomenclature for Impact Forces

4.4.5 Impacts and Collisions

aavg | average deceleration
K(e) | kinetic energy
P(e) | potential energy
t | time of impact
v(impact) | impact velocity
m | mass
g | gravitational acceleration
v(f inal) | final velocity
l(m) | impulse
F | impact force

Page 52

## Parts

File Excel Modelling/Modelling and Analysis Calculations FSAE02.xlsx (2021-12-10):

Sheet: COFM
Component | x (mm) | y (mm) | z (mm) | Mass (kg) | x *mass | y * mass | z * mass | m | 303.465
Chassis: | 0 | 246.9 | 1345.2 | 38.56 | 0 | 9520.464 | 51870.912 | a2 | 0.7898887495 |  | 0.002765063516
Battery: | 0 | 94.11 | 1910.3 | 30.38 | 0 | 2859.0618 | 58034.914 | a1 | 0.8131362505
Front Left Wheel Assembly: | 500 | 97.27 | 658.535 | 9.843 | 4921.5 | 957.42861 | 6481.960005 | h | 0.2891896851
Front Right Wheel Assembly: | -500 | 97.27 | 658.535 | 9.843 | -4921.5 | 957.42861 | 6481.960005 | lf | 0.8631362505
Rear Left Wheel Assembly: | 500 | 97.27 | 2261.56 | 13.843 | 6921.5 | 1346.50861 | 31306.77508 | lr | 0.8198887495
Rear Right Wheel Assembly: | -500 | 97.27 | 2261.56 | 13.843 | -6921.5 | 1346.50861 | 31306.77508 | hf | 0.1891896851
Driver: | 0 | -35 | 1312.54 | 111.58 | 0 | -3905.3 | 146453.2132 | hr | 0.9958103149
Motor and big sprocket: | 100 | -9 | 2201 | 12 | 1200 | -108 | 26412 | bleft | 0.4972349365
Steering Assembly: | 0 | 183.24 | 658.535 | 11.796 | 0 | 2161.49904 | 7768.07886 | brigjt | 0.5027650635
Seat and Harness: | 0 | 485 | 1830 | 3.85 | 0 | 1867.25 | 7045.5
Rear drive shaft: | 0 | 183.24 | 2261.56 | 10.933 | 0 | 2003.36292 | 24725.63548
Front Suspension Assembly: | 0 | 550 | 645.72 | 10.656 | 0 | 5860.8 | 6880.79232
Rear Suspension Assembly: | 0 | 650 | 2050 | 16.712 | 0 | 10862.8 | 34259.6
Pedal Box: | -150 | 100 | 100 | 2.406 | -360.9 | 240.6 | 240.6
Rear wing and mouting: | 0 | 1021.56 | 1950 | 3.76 | 0 | 3841.0656 | 7332
Front Splitter and mouting: | 0 | 0 | 0 | 3.46 | 0 | 0 | 0
Total Mass |  |  |  | 303.465 | 839.1 | 39811.4778 | 446600.716
COM | 2.765063516 | 131.1896851 | 1471.67125
 | Origin is in the middle of Front Bulkhead |  |  |  |  |  |  |  |  | SPRUNG MASS | 223.2585
 |  |  |  |  |  |  |  |  |  | UNSPRUNG MASS | 80.2065
COM from Ground | 2.765063516 | 289.1896851 | 1471.67125
 |  |  |  |  |  |  |  |  |  |  | 303.465
 |  |  |  | Rear Tire to COFM | Front Tire to COFM
 |  |  | -789.8887495 |  | 813.1362505
 |  |  |  |  | 1603.025

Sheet: Kinematic Models
ACCELERATION CALC |  |  |  | DECELERATION CALC |  |  |  |  | SPEED VS CORNERING RADIUS |  |  |  |  |  | 1 | in | 0.0254 | m
Height from Road to COFM | h | 0.2891896851 | m | Height from Road to COFM | h | 0.2891896851 | m |  | Height from Road to COFM | h | 0.2891896851 | m | 2235.529053 |  | m | 303.465 | kg
Length from COFM to Front | a1 | 0.8131362505 | m | Length from COFM to Front | a1 | 0.8131362505 | m |  | Length from COFM to Front | a1 | 0.8131362505 | m |  |  | a2 | 0.7898887495 | m
Length from COFM to Rear | a2 | 0.7898887495 | m | Length from COFM to Rear | a2 | 0.7898887495 | m |  | Length from COFM to Rear | a2 | 0.7898887495 | m |  |  | a1 | 0.8131362505 | m
Mass of the Vehicle | m | 303.465 | kg | Length from COFM to Rear Wing | l_r | 0.8198887495 | m |  | Length from Right Wheel to COFM | b | 0.4972349365 | m |  |  | h | 0.2891896851 | m
Acceleration due to gravity | g | 9.81 | m/s^2 | Length from COFM to Front Wing | l_f | 0.8631362505 | m |  | Length from Left Wheel to COFM | b | 0.5027650635 | m |  |  | lf | 0.8631362505 | m
Radius of the Tire | Rw | 0.25527 | m | Mass of the Vehicle | m | 303.465 | m |  | Mass of the Vehicle | m | 303.465 | kg |  |  | lr | 0.8198887495 | m
Peak Power Batter | Pb | 70.56 | kW | Coefficient of Drag | C_D | 0.92 |  |  | Acceleration due to gravity | g | 9.81 | m/s^2 |  |  | hf | 0.1891896851 | m
Max Torque from Motor | Tm | 140.0340426 | Nm | Acceleration due to gravity | g | 9.81 | m/s^2 |  | Radius of the Tire | Rw | 0.25527 | m |  |  | hr | 0.9958103149 | m
Number of Teeth Driving | N1 | 14 |  | Radius of the Tire | Rw | 0.25527 | m |  | Total Normal Force on Front Wheels | WF | 1466.909257 | N | Statics |  | b_left | 0.4972349365 | m
Number of Teeth Driven | N2 | 35 |  | Maximum Down Force Generated | F_TL | 1880.095547 | N |  | Total Normal Force on Rear Wheels | WR | 1510.082393 | N | Statics |  | b_right | 0.5027650635 | m
Differential Gear Ratio | DGR | 1 | 1 | Lift Generated from Car | F_LC | 232.8824106 | N |  | Front Bias | blad | 0.4927488651 | 1466.909257
Transmission Efficiency | n_Tr | 0.92 |  | Height from COFM to Front Wing | h_f | 0.1891896851 | m | 1647.213136 | Rear Bias | blod | 0.5072511349 | 1510.082393
Coefficient of Friction (Road) | u_f | 0.9 |  | Height from COFM to Rear Wing | h_r | 0.9958103149 | m |  | Aero without velocity | rho*cd*A | 2.2089249
 |  |  |  | Coefficient of Friction (Road) | u_f | 0.9 |  |  | Front Normal Force on Right Wheel | F_Nfr | 354.3429387 | N | Smallest Corner
 |  |  |  | Finding maximum allowable deceleration due to friction |  |  |  |  | Front Normal Force on Left Wheel | F_Nfl | 1122.176201 | N
Finding max accel of car from the motor |  |  |  | Total Normal Force about COFM | F_NT | 4624.204786 | N |  | Rear Normal Force on Right Wheel | F_Nrr | 364.7717337 | N
Torque transferred to wheels | T_w | 322.0782979 | Nm | Maximum allowable total Friction from Tires and Road | F_fmax | 4161.784308 | N |  | Rear Normal Force on Left Wheel | F_Nrl | 1155.203374 | N
Force transmitted from the wheels | F_w | 1261.716214 | N | Thus max decel. Allowed |  |  |  |  | Friction Verification |  | 2696.844823 | N
Max Allowable Total Friction from Tires and the Road |  |  |  | Maximum Deceleration | a_decel max | 13.71421517 | m/s^2 |  | Front Normal Force on Right Wheel | F_Nfr | 519.8019781 | N | Largest Corner Multiplied by BIAS
Friction Force from tires to road | F_f | 2679.292485 | N | Maximum Deceleration in G's | a/g | 1.397983198 | g |  | Front Normal Force on Left Wheel | F_Nfl | 1661.655659 | N
Since F_f > F_w, car will accelerate wihtout slip |  |  |  | Time Required to Stop from Max Speed to 0 | t_stopping | 2.12674705 | s |  | Rear Normal Force on Right Wheel | F_Nrr | 535.1004578 | N
Thus, |  |  |  | Estimated Stopping Distance | S_stopping | 31.01506115 | m |  | Rear Normal Force on Left Wheel | F_Nrl | 1710.560447 | N
Max Acceleration of the Car | a_max | 4.157699286 | m/s^2 |  |  |  |  |  | Friction Verification |  | 3984.406688 | N
INDUCED FROM A STAND STILL AS THERE ARE LITTLE TO NO DRAG FORCES INDUCED ON THE VEHICLE THIS ACCELERATION IS UNATTAINABLE SMALLER MOTOR REQUIRED |  |  |  | Drag? Will be ADDED tmrw max |  |  |  |  |  | 3372.216106 | 1054.902436 | 0.3128217181 | 0.6871782819 | R
 |  |  |  |  |  |  |  |  | Reaction Forces at wheel due to F_C right | F_yr | 1246.408946 | N | DON’T USE
 |  |  |  |  |  |  |  |  | Reaction Forces at wheel due to F_C left | F_yl | 2737.997742 | N
Force Reactions Due to Acceleration |  |  |  | Force Reactions Due to Decceleration |  |  |  |  | Reaction Forces at wheel due to F_C Front right | F_yfr | 614.1665934 | N
Sum of Forces about Z-axis |  |  |  |  |  |  |  |  | Reaction Forces at wheel due to F_C Rear right | F_yrr | 632.2423521 | N
 |  |  |  | Height from Road to COFM | h | 0.2891896851 | m |  | Reaction Forces at wheel due to F_C Front left | F_yfl | 1349.14528 | N | Largest Corner Multiplied by BIAS
Height from Road to COFM | h | 0.2891896851 | m | Length from COFM to Front | a1 | 0.8131362505 | m |  | Reaction Forces at wheel due to F_C Rear left | F_yrl | 1388.852462 | N
Length from COFM to Front | a1 | 0.8131362505 | m | Length from COFM to Rear | a2 | 0.7898887495 | m |  | Friction Forces Front Left | F_xfl | 1495.490093 | N | Largest Corner Multiplied by BIAS
Length from COFM to Rear | a2 | 0.7898887495 | m | Length from COFM to Rear Wing | l_r | 0.8198887495 | m |  | Friction Forces Rear Left | F_xrl | 1539.504402 | N
Mass of the Vehicle | m | 303.465 | kg | Length from COFM to Front Wing | l_f | 0.8631362505 | m |  | Friction Forces Front right | F_xfr | 467.8217803 | N | Largest Corner Multiplied by BIAS
Acceleration due to gravity | g | 9.81 | m/s^2 | Mass of the Vehicle | m | 303.465 | kg |  | Friction Forces Rear right | F_xrr | 481.590412 | N
Normal Force on a Front Wheel | Fz_f | 619.6462616 | N | Acceleration due to gravity | g | 9.81 | m/s^2 |  | TOTAL FORCE ON FRONT LEFT
Normal Force on a Rear Wheel | Fz_r | 868.8495634 | N | Maximum Deceleration | a_decel max | 13.71421517 | m/s^2
Normal Force Front | 2*Fz_f | 1239.292523 | N | Coefficient of Lift Rear Wing | C_ff | 3.074 | ASSUMED DON’T KNOW HOW TO FINDING NEED SAPPORT |  | F_Tfl | 2611.088496 |  |  |  | Largest Corner Multiplied by BIAS
Normal Force Rear | 2*Fz_r | 1737.699127 | N | Coefficient of Lift Front Wing | C_fr | 3.074 |  |  | TOTAL FORCE ON REAR LEFT
Verification of Friction Force | F_f | 2083.894155 | N | Coefficient of Lift Car | C_fcar | 0.29
 |  |  |  | Frontal Area of Front Wing | A_f | 0.5312 | m^2 |  | F_Trl | 2687.936384 |  |  |  | Largest Corner Multiplied by BIAS
 |  |  |  | Frontal Area of Rear Wing | A_r | 0.6425 | m^2
Force Reactions Due to Acceleration Method 2 ex.107 FVD Springer |  |  |  | Frontal Area of Car | A_car | 1.5412 | m^2 |  | VELOCITY ITTERATIONS
 |  |  |  | Density of Air | p | 1.225 | kg/m^3 |  | Coefficient of Lift for Car | C_lcar | 2.34 |  | DOWNWARDS
Height from Road to COFM | h | 0.2891896851 | m | Maximum Velocity of Vehicle | v_max | 29.16666667 | m/s |  | Frontal Area of Car | A_car | 1.5412 | m^2
Length from COFM to Front | a1 | 0.8131362505 | m | Downforce Produced by Front Wing | F_lf | 850.8276972 | N | Downwards | Density of Air | p | 1.225 | kg/m^3
Length from COFM to Rear | a2 | 0.7898887495 | m | Downforce Produced by Rear Wing | F_lr | 1029.097883 | N | Downwards | Downforce Produced | F_l | ? | N
Mass of the Vehicle | m | 303.465 | kg | Lift Force Produced from Car | F_lcar | 232.8824106 | N | Upwards | Mass of the Vehicle | m | 303.465 | kg
Acceleration due to gravity | g | 9.81 | m/s^2 | Drag Force Front | F_Df | 262.4119113 | N |  | Coefficient of Friction |  | 0.9
Max Acceleration 1 | a_1 | 5.346607376 | m/s^2 | Drag Force Rear | F_Dr | 216.9544082 | N |  | Gravity |  | 9.81
Acceleration for WHEELIES | a_2 | 26.79489979 | m/s^2 | Total Drag | F_D | 603.1015278 | N |  |  | Cornering Radius (m) | Max Velocity (m/s) | F_c | F_friction
Normal Force on a Front Wheel | Fz_f | 587.1023765 | N |  | C_Davg | 0.7838459572 |  |  |  | 1 | 2.971363323 | 2679.292485 | 2696.844823
Normal Force on a Rear Wheel | Fz_r | 901.3934485 | N | Normal Force on a Front Wheel | Fz_f | 1548.7543 | N | Downforce only |  | 2 | 4.229944508 | 2714.863217 | 2714.863217
Normal Force Front | 2*Fz_f | 1174.204753 | N | Normal Force on a Rear Wheel | Fz_r | 763.26311 | N |  |  | 3 | 5.197883559 | 2733.005132 | 2733.005132
Normal Force Rear | 2*Fz_r | 1802.786897 | N | Normal Force Front | 2*Fz_f | 3097.5086 | N |  |  | 4 | 6.022154018 | 2751.391142 | 2751.391142
Friction Force | F_f | 2083.894155 | N | Normal Force Rear | 2*Fz_r | 1526.52622 | N |  |  | 5 | 6.755735483 | 2770.026208 | 2770.026208
Friction Force From Rear Wheels | F_fr | 1622.508207 | N | Total Normal Forces Acting on Car | Fz_T | 4624.03482 | N |  |  | 6 | 7.42572724 | 2788.915425 | 2788.915425
 |  |  |  | Verification of Friction Force | F_f | 4161.631338 | N |  |  | 7 | 8.048189961 | 2808.064027 | 2808.064027
 |  |  |  | Normal Force on a Front Wheel | Fz_f | 1688.747366 | N | Downforce and Drag |  | 8 | 8.633566921 | 2827.477395 | 2827.477395
Static Scenrio |  |  |  | Normal Force on a Rear Wheel | Fz_r | 637.1518955 | N |  |  | 9 | 9.189099784 | 2847.161057 | 2847.161057
Normal Force Front | 2*Fz_f | 1466.909257 | N | Normal Force Front | 2*Fz_f | 3377.494733 | N |  |  | 10 | 9.720054129 | 2867.120698 | 2867.120698
Normal Force Rear | 2*Fz_r | 1510.082393 | N | Normal Force Rear | 2*Fz_r | 1274.303791 | N |  |  | 11 | 10.23040127 | 2887.362164 | 2887.362164
Normal Force Front | Fz_f | 733.4546285 | N | Total Normal Forces Acting on Car | Fz_T | 4651.798524 | N |  |  | 12 | 10.72322491 | 2907.891466 | 2907.891466
Normal Force Rear | Fz_r | 755.0411965 | N | Verification of Friction Force | F_f | 4186.618671 | N |  |  | 13 | 11.20097716 | 2928.714787 | 2928.714787
 |  |  |  |  |  |  |  |  |  | 14 | 11.66564704 | 2949.83849 | 2949.83849
 |  |  |  |  |  |  |  |  |  | 15 | 12.11887538 | 2971.26912 | 2971.26912
 |  |  |  |  |  |  |  |  |  | 16 | 12.56203557 | 2993.013418 | 2993.013418
 |  |  |  |  |  |  |  |  |  | 17 | 12.99629184 | 3015.078319 | 3015.078319
 |  |  |  |  |  |  |  |  |  | 18 | 13.42264227 | 3037.470967 | 3037.470967
 |  |  |  |  |  |  |  |  |  | 19 | 13.84195109 | 3060.19872 | 3060.19872
 |  |  |  |  |  |  |  |  |  | 20 | 14.25497344 | 3083.269155 | 3083.269155
 |  |  |  |  |  |  |  |  |  | 21 | 14.66237452 | 3106.690083 | 3106.690083
 |  |  |  |  |  |  |  |  |  | 22 | 15.06474476 | 3130.469551 | 3130.469551
 |  |  |  |  |  |  |  |  |  | 23 | 15.46261186 | 3154.615857 | 3154.615857
 |  |  |  |  |  |  |  |  |  | 24 | 15.85645049 | 3179.137554 | 3179.137554
 |  |  |  |  |  |  |  |  |  | 25 | 16.2466902 | 3204.043466 | 3204.043466
 |  |  |  |  |  |  |  |  |  | 26 | 16.63372191 | 3229.342693 | 3229.342693
 |  |  |  |  |  |  |  |  |  | 27 | 17.01790328 | 3255.044627 | 3255.044627
 |  |  |  |  |  |  |  |  |  | 28 | 17.39956323 | 3281.15896 | 3281.15896
 |  |  |  |  |  |  |  |  |  | 29 | 17.77900568 | 3307.695699 | 3307.695699
 |  |  |  |  |  |  |  |  |  | 30 | 18.15651279 | 3334.665175 | 3334.665175
 |  |  |  |  |  |  |  |  |  | 31 | 18.53234765 | 3362.07806 | 3362.07806
 |  |  |  |  |  |  |  |  |  | 32 | 18.90675668 | 3389.945381 | 3389.945381
 |  |  |  |  |  |  |  |  |  | 33 | 19.27997157 | 3418.278532 | 3418.278532
 |  |  |  |  |  |  |  |  |  | 34 | 19.6522111 | 3447.089291 | 3447.089291
 |  |  |  |  |  |  |  |  |  | 35 | 20.02368264 | 3476.389839 | 3476.389839
 |  |  |  |  |  |  |  |  |  | 36 | 20.39458351 | 3506.19277 | 3506.19277
 |  |  |  |  |  |  |  |  |  | 37 | 20.76510213 | 3536.511119 | 3536.511119
 |  |  |  |  |  |  |  |  |  | 38 | 21.13541909 | 3567.358372 | 3567.358372
 |  |  |  |  |  |  |  |  |  | 39 | 21.5057081 | 3598.748491 | 3598.748491
 |  |  |  |  |  |  |  |  |  | 40 | 21.8761368 | 3630.695933 | 3630.695933
 |  |  |  |  |  |  |  |  |  | 41 | 22.2468675 | 3663.215675 | 3663.215675
 |  |  |  |  |  |  |  |  |  | 42 | 22.61805791 | 3696.323234 | 3696.323234
 |  |  |  |  |  |  |  |  |  | 43 | 22.9898617 | 3730.034692 | 3730.034692
 |  |  |  |  |  |  |  |  |  | 44 | 23.36242911 | 3764.366725 | 3764.366725
 |  |  |  |  |  |  |  |  |  | 45 | 23.73590743 | 3799.336628 | 3799.336628
 |  |  |  |  |  |  |  |  |  | 46 | 24.11044151 | 3834.962344 | 3834.962344
 |  |  |  |  |  |  |  |  |  | 47 | 24.48617418 | 3871.262497 | 3871.262497
 |  |  |  |  |  |  |  |  |  | 48 | 24.8632467 | 3908.25642 | 3908.25642
 |  |  |  |  |  |  |  |  |  | 49 | 25.24179909 | 3945.964196 | 3945.964196
 |  |  |  |  |  |  |  |  |  | 50 | 25.62197056 | 3984.406688 | 3984.406688

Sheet: Brake System Pedal to Wheel
Front and Rear Tire Brake Analysis
Vehicle Properties |  |  |  |  | m | 303.465
Gravity | g | 9.81 | m/s^2 |  | a2 | 0.7898887495
Mass of Vehicle | m_v | 303.465 | kg |  | a1 | 0.8131362505
Radius of Wheel | R_w | 0.25527 | m | Modelling Report | h | 0.2891896851
Maximum Vehicle Velocity | V_max | 29.1667 | m/s | 105 km/h | lf | 0.8631362505
Angular Velocity of the Wheel at max velocity | omega_max | 114.2582364 | rad/s |  | lr | 0.8198887495
Coefficient of Friction Between Tire and Road | mu_road | 0.9 |  |  | hf | 0.2191896851
Normal Force on Wheel Front for 1 Tire | F_NF1 | 1688.747366 | N | From Deceleration Analysis | hr | 0.9958103149
Normal Force on Wheel Front for 1 Tire | F_NF2 | 1688.747366 | N | From Deceleration Analysis | bleft | 0.4972349365
Normal Force on Wheel Rear for 1 Tire | F_NR1 | 637.1518955 | N | From Deceleration Analysis | brigjt | 0.5027650635
Normal Force on Wheel Rear for 1 Tire | F_NR2 | 637.1518955 | N | From Deceleration Analysis
Pedal Forces & Bias Bar Translations
 |  |  |  |  |  | PARAM. C LENGTH ATTACHMENT POINT TO ROD AND BIAS RATIOS + SAFETY FACTOR FOR LOCKING
Description | Variable | Value | Units | Notes
Length at which Pedal Force is Applied from Pinion | L | 0.125 | m
Length at which Master Cylinders attach to pedal from Pinion | C | 0.036 | m | Variable we can change
Force Applied by Drivers Foot | Fapp | 300 | N
Reaction force from Master Cylinder Rod | Fc | 1041.666667 | N
Bias Bar Front Ratio | BBRf | 0.57 | - | Variable we can change
Bias Bar Rear Ratio | BBRr | 0.43 | - | Variable we can change |  | Master Cylinders
Front Master Cylinder Bore Radius | R_FMC | 0.0079375 | m | 5/8 " Master Cylinder |  | https://www.wilwood.com/MasterCylinders/MasterCylinderProd?itemno=260-10371
Rear Master Cylinder Bore Radius | R_RMC | 0.0111125 | m | 7/8 " Master Cylinder |  | https://www.wilwood.com/MasterCylinders/MasterCylinderProd?itemno=260-10374
Front Master Cylinder Force | F_FMC | 593.75 | N
Rear Master Cylinder Force | F_RMC | 447.9166667 | N
Caliper and Rotor Specs Front
Radius of Front Caliper Pistons | R_CPPf | 0.015875 | m | Refer to Wilwoods Subject to change
Equivelant Radius of Front Calipers from Center Wheel | R_ef | 0.125349 | m
Coefficient of Friction between Pads and Disc/Rotor | mu_pd | 0.37 |  | Shgileys
Rotor Width | t_rotorf | 0.0127 | m | Refer to Wilwoods Subject to change
Rotor/Disc Radius | R_rotorf | 0.1397 | m
Forces Acting on Front Brakes at Max Deceleration
Area of Front Master Cylinder | A_MCf | 0.0001978322656 | m^2
Area of Front Caliper Pistons | A_Calf | 0.0007913290625 | m^2
Normal Force Applied on 1 Caliper Piston | F_Ncalf | 2375 | N |  |  | CALIPERS
Number of Pistons for the Front Caliper | n | 4 |  |  |  | https://www.wilwood.com/PDF/Flyers/fl148.pdf
Total Froce Applied on Caliper Pistons | F_Tncalf | 9500 | N |  |  | https://www.wilwood.com/Calipers/CaliperProd?itemno=120-15752%20%20%20%20%20%20&appid=0
Total Friction Force Front Calipers Apply on Rotor | F_fcalf | 3515 | N
Total Friction Force from Front Tire | F_ff | 1519.87263 | N
Torque applied from front Calipers onto Rotor | T_calf | 440.601735 | N.m | T_caf > T_ff thus wheels will lock!
Torque from Friction at Front Tire | T_ff | 387.9778862 | N.m
Caliper and Rotor Specs Rear
Radius of Rear Caliper Pistons | R_CPPr | 0.015875 | m | Refer to Wilwoods Subject to change
Equivelant Radius of Rear Calipers from Center Wheel | R_er | 0.125349 | m
Coefficient of Friction between Pads and Disc/Rotor | mu_pd | 0.37 |  | Shgileys |  | Rotor Dimensions determined from Calipers and equivelant found
Rotor Width | t_rotorr | 0.0508 | m | Refer to Wilwoods Subject to change |  | https://www.wilwood.com/Calipers/CaliperProd?itemno=120-15752%20%20%20%20%20%20&appid=0
Rotor Radius | R_rotorr | 0.14605 | m |  |  | https://www.wilwood.com/Rotors/RotorProd?itemno=160-10662-BK%20%20%20&appid=0
Forces Acting on Rear Brakes at Max Deceleration
Area of Front Master Cylinder | A_MCr | 0.0003877512406 | m^2
Area of Front Caliper Pistons | A_Calr | 0.0007913290625 | m^2
Normal Force Applied on 1 Caliper Piston | F_Ncalr | 914.1156463 | N
Number of Pistons for the Front Caliper | n | 4
Total Froce Applied on Caliper Pistons | F_Tncalr | 3656.462585 | N
Total Friction Force Front Calipers Apply on Rotor | F_fcalr | 1352.891156 | N
Total Friction Force from Front Tire | F_fr | 573.4367059 | N
Torque applied from front Calipers onto Rotor | T_calr | 169.5835536 | N.m | T_caf > T_ff thus wheels will lock!
Torque from Friction at Front Tire | T_fr | 146.3811879 | N.m
Yield Stress Analysis
Area of Pads at which caliper force is applied on to rotors | A_pads | 0.002354834 | m^2 | Refer to Wilwoods Caliper Properties
Highest Normal Force applied on Rotors | F_Ncal | 9500 | N
Induced Stress on Rotors from Normal Force Applied | sigma | 4.034254644 | MPa
Yield Strength of Stainless Steel | Sy | 276 | MPa
Safety factor | n | 68.41412463
PEDAL BOX DESIGN ANALYSIS (RETURN SPRING BRAKES)
Max Force Applied from Drivers Foot | F_app | 300 | N
Force Applied from Master Cylinders into pedal | F_C | 1041.666667 | N
Reaction Moment from Spring | M_s | 4.974147346 | Nm
Length at which Pedal Force is Applied from Pinion | L | 0.125 | m
Length at which Master Cylinders attach to pedal from Pinion | C | 0.036 | m
Theta Angle at which the force changes the pedal position | theta | 0.3663333333 | radians
Distance horizontally from joint to F_cy | a | 0.02 | m

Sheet: Pedal Box Design
Front and Rear Tire Brake Analysis
Vehicle Properties |  |  |  |  |  |  | m | 303.465
Gravity | g | 9.81 | m/s^2 |  |  |  | a2 | 0.7898887495
Mass of Vehicle | m_v | 303.465 | kg |  |  |  | a1 | 0.8131362505
Radius of Wheel | R_w | 0.25527 | m | Modelling Report |  |  | h | 0.2891896851
Maximum Vehicle Velocity | V_max | 29.1667 | m/s | 105 km/h |  |  | lf | 0.8631362505
Angular Velocity of the Wheel at max velocity | omega_max | 114.2582364 | rad/s |  |  |  | lr | 0.8198887495
Coefficient of Friction Between Tire and Road | mu_road | 0.9 |  |  |  |  | hf | 0.2191896851
Normal Force on Wheel Front for 1 Tire | F_NF1 | 1688.747366 | N | From Deceleration Analysis |  |  | hr | 0.9958103149
Normal Force on Wheel Front for 1 Tire | F_NF2 | 1688.747366 | N | From Deceleration Analysis |  |  | bleft | 0.4972349365
Normal Force on Wheel Rear for 1 Tire | F_NR1 | 637.1518955 | N | From Deceleration Analysis |  |  | brigjt | 0.5027650635
Normal Force on Wheel Rear for 1 Tire | F_NR2 | 637.1518955 | N | From Deceleration Analysis
Pedal Forces & Cable Translations
 |  |  |  |  | w
Description | Variable | Value | Units | Notes
PEDAL BOX DESIGN ANALYSIS (RETURN SPRING Accel Pedal)
Min Force Applied from Drivers Foot | F_appmin | 45 | N
Force Applied from Cable into pedal | F_C | 10 | N | CABLE FORCE NOT FROM MC
Max Force Applied from Drivers Foot | F_appmax | 300 | N
Reaction Moment from Spring | M_s | 5.217248185 | Nm
Length at which Pedal Force is Applied from Pinion | L | 0.125 | m
Length at which Master Cylinders attach to pedal from Pinion | C | 0.036 | m
Theta Angle at which the force changes the pedal position | theta | 0.3663333333 | radians
Distance horizontally from joint to F_cy | a | 0.02 | m |  |  | W
Spring Force Max | F_s1 | 1854.612409 | N
Spring Design and Analysis
Spring Width | d | 0.009 | m | Same spring will be used for brake pedal No point in designing two different ones
Angle between horizontal to spring arm L1 | Beta | 180 | degrees
Inner Diameter | ID | 0.02 | m
Outer Diameter | D | 0.029 | m
Length of arm at which F_s1 is applied | L1 | 0.02 | m
Length of arm at which F_s2 reacts | L2 | 0.03 | m
Max spring force from Pedal | F_s1 | 1854.612409 | N
Spring Reaction Force | F_s2 |  | N
Total Angular Deflection | Theta_t | 0.0412361768 | radians
Young's Modulus | E | 203400000000 | Pa
Spring Rate | K | 126.5211421 | Nm/rad
Body Turn Count | N_b | 5.5 | turns
Ultimate Tensile Stress | S_ut | 1445898830 | Pa
Yield Stress | S_y | 1257931982 | Pa
Spring Index | C | 3.222222222
Bending Stress Factor | K_i | 1.302586207
Bending Stress | sigma | 675433246.8 | Pa
Safety Factor | n | 1.862407555
Spring Fatigue Analysis
Max Moment | M_max | 37.09224819 | Nm
Min Moment | M_min | 5.217248185 | Nm
Amplitude of Moments | M_a | 15.9375 | Nm
Stress amplitude | sigma_a | 290214745.6 | Pa | 290.2147456
Mean Moment | M_m | 21.15474819 | Nm
Stress mean | sigma_m | 385218501.2 | Pa | 385.2185012
Fatigue Strength | S_f | 925375251.1 | Pa | 925.3752511
Corrected Fatigue Strength | S_fc | 515471953.6 | Pa | 515.4719536
Safety Factor | n_f | 1.567109905

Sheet: Sheet1
Assembly | Component | Optimization
Chassis | Pipe A Thickness | 6.5 mm < t < 8.1 mm
Chassis | Square Pipe B Thickness | 5.2 mm < t < 6 mm
Control Arm Tubes | Inner Diameter | < ID <
Spring | Wire Diameter | < D_{wire} <
Spring | Mean Coil Diameter | < D_{mean coil} <
Damper | Outer Diameter Piston | <D_{Piston Outer} <
Damper | Piston Wall thickness | <t_{Piston Wall} <
Damper | Orifice Diameter | < D_{Orifice} <
Steering | Rack Length | < L_{rack} <
Steering | Shaft Inner Diameter | < ID <
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

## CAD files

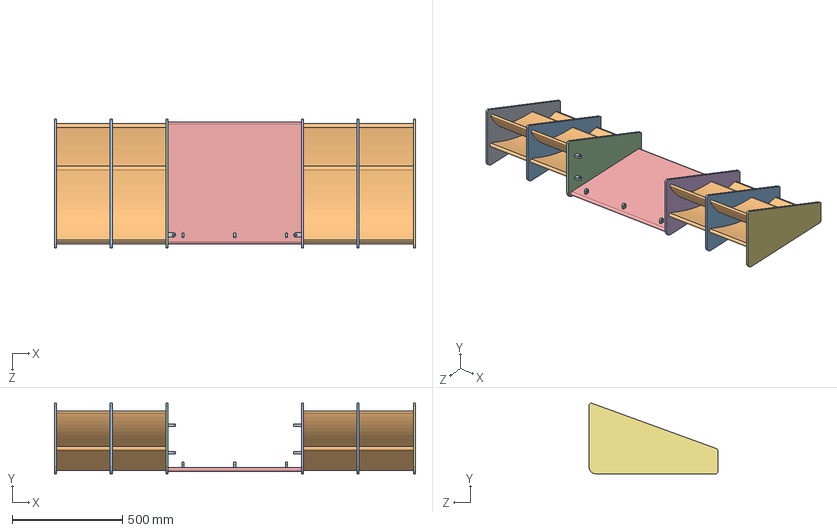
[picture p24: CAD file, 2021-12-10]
Solidworks/Front Wing/Front Wing.SLDASM
1635.0 x 319.9 x 583.8 mm
Left Plate
Front Flaps x 2
Middle Plate x 2
Right Mid Plate
Bottom Plate
Left Mid Plate
Right Plate
Front Wing Bottom Mount x 3
Front Wing Side Mount x 4

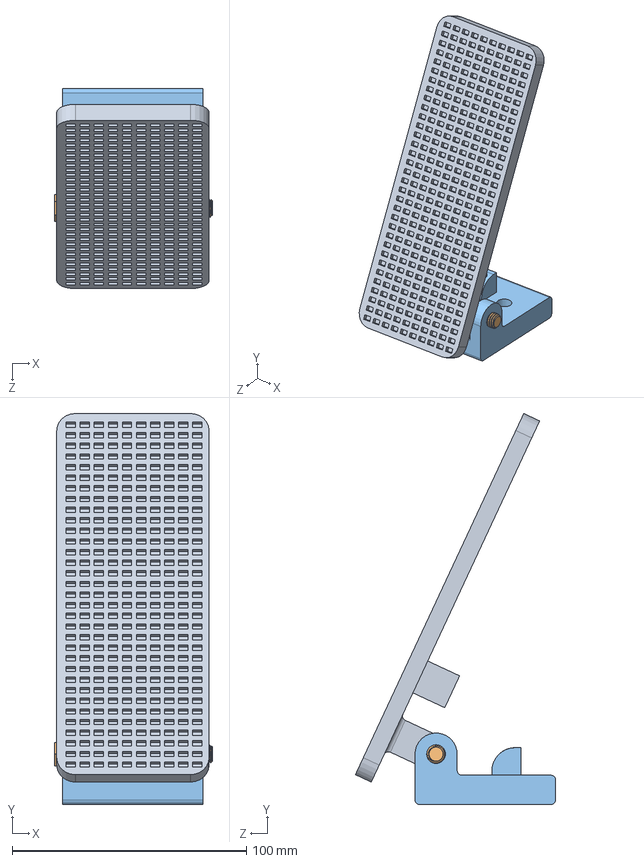
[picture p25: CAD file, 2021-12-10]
Solidworks/Pedal Box/Throttle Pedal.SLDASM
67.5 x 166.8 x 85.4 mm
Pedal
Pivot Pin
Throttle Pedal Base Plate

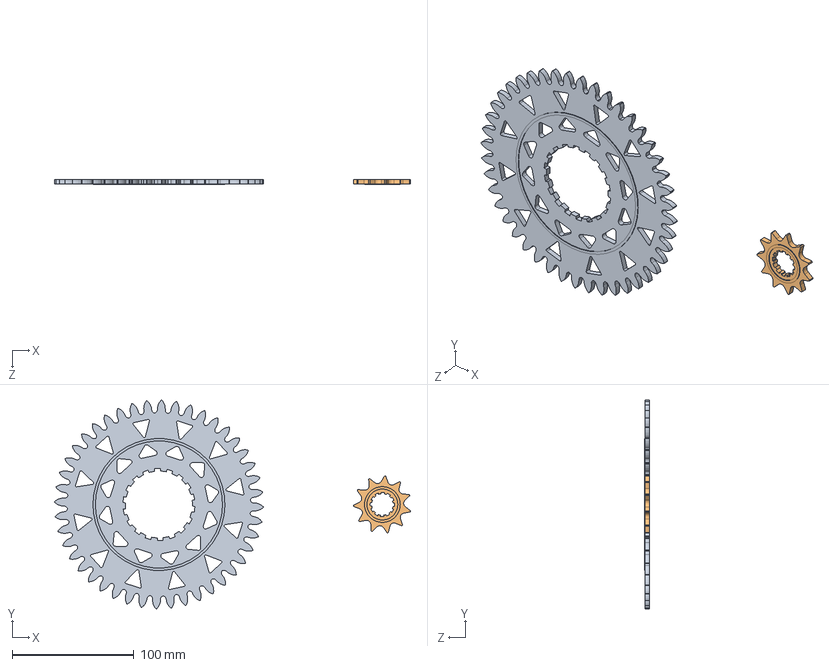
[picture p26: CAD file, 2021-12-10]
Solidworks/Powertrain/Chain and Sprocket/Chain_Sprocket_Assembly.SLDASM
292.0 x 171.3 x 4.50 mm
Big_Sprocket
Small_Sprocket

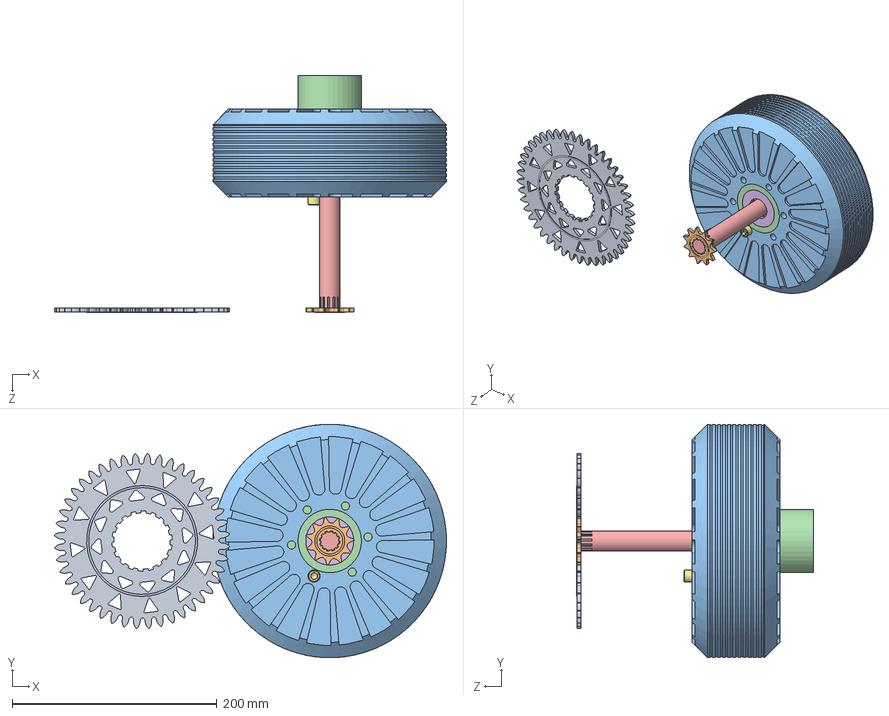
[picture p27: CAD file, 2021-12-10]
Solidworks/Powertrain/Motor/Motor_Chain_Assembly.SLDASM
382.8 x 227.8 x 231.7 mm
Big_Sprocket
Small_Sprocket
Motor_Rotor
Motor_Inner
Motor_Shaft
thrust ball bearing3_68_am x 2
socket head cap screw_ai

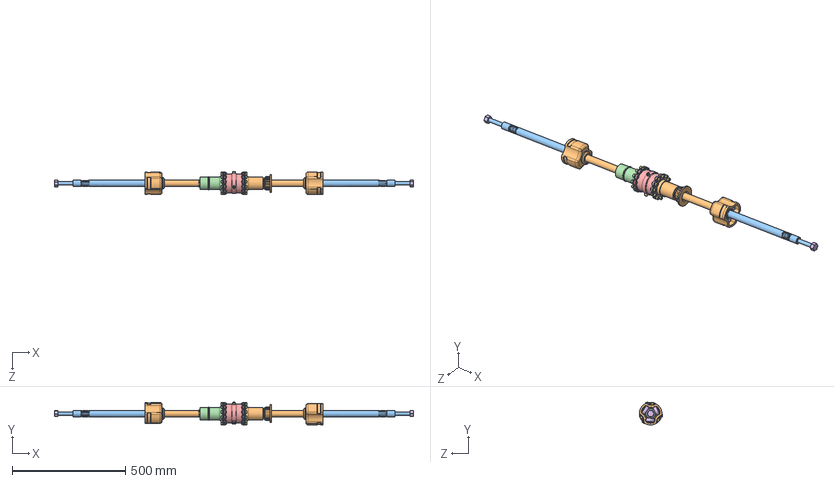
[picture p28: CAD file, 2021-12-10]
Solidworks/Powertrain/Rear_Axle_Assembly.SLDASM
1582.6 x 101.3 x 102.9 mm
Tripod_Spider x 2
Tripod_Shaft x 2
Half_Axle_Shaft x 2
Needles x 6
RE x 6
Roller x 6
Bevel_Gear x 2
Spider_Gear x 4
Spider_Pin
Sprocket_Diff_Housing
Clutch_Plate x 10
Output_Housing
Housing_Middle
Rim_Nut x 2
socket head cap screw_ai x 27

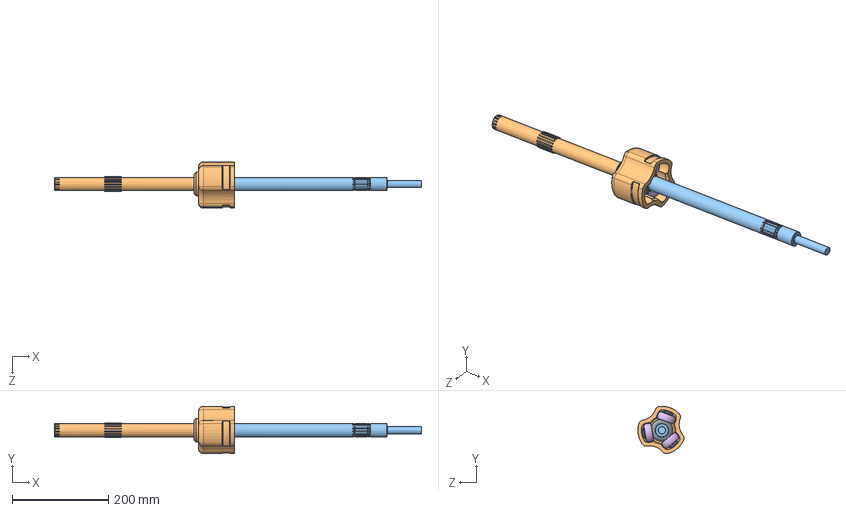
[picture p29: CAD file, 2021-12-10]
Solidworks/Powertrain/Tripod and Half Axle/Tripod_Half_Axle_Assembly.SLDASM
764.3 x 98.8 x 96.4 mm
Tripod_Spider
Tripod_Shaft
Half_Axle_Shaft
Needles x 3
RE x 3
Roller x 3

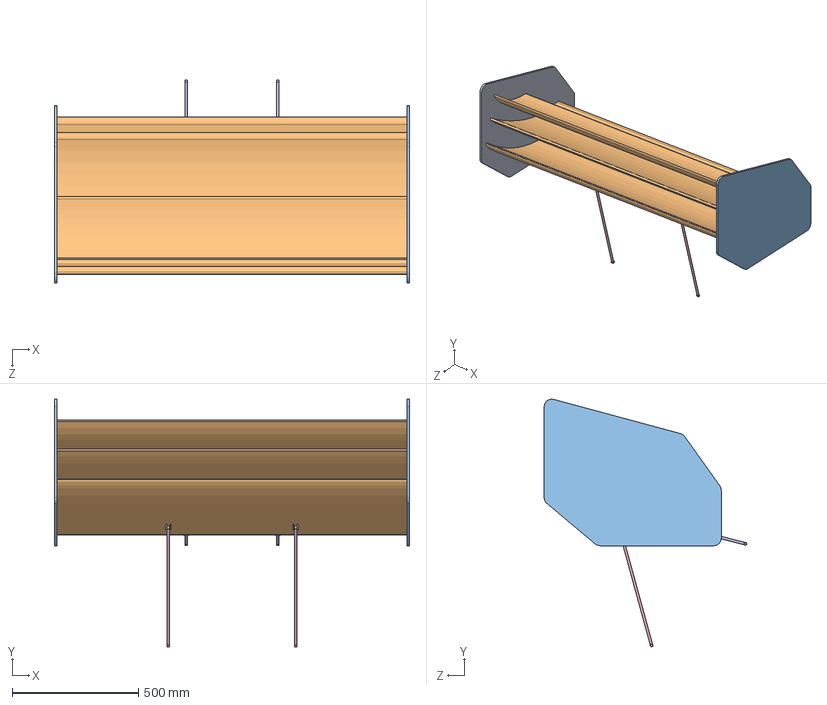
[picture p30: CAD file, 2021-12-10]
Solidworks/Rear Wing/Rear Wing.SLDASM
1406.0 x 981.0 x 802.7 mm
Left Endplate
Flaps
Right Endplate
Rear Wing Mounts
Lower Mounting Bar x 2
Upper Mounting Bar x 2

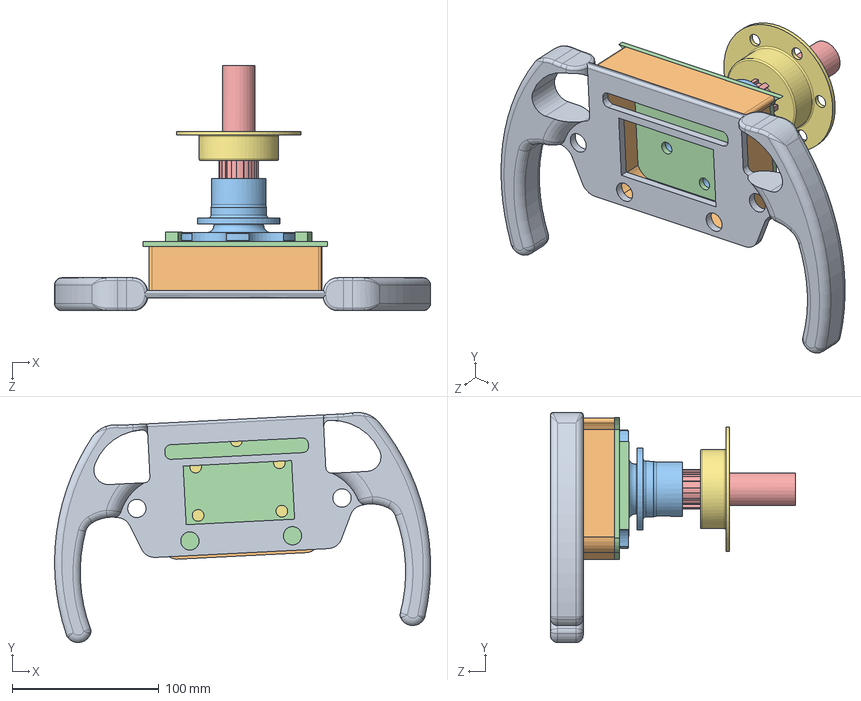
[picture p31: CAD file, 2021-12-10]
Solidworks/Steering/Updated Steering/Steering Wheel/Steering Assembley.SLDASM
256.2 x 156.8 x 167.2 mm
Steering_Wheel
Back Plate
Quick Release Hub
Back Plate Attachment to Quick Release Hub
Steering Shaft Input
thrust ball bearing2_ai
Quick Release Chassis Attachment

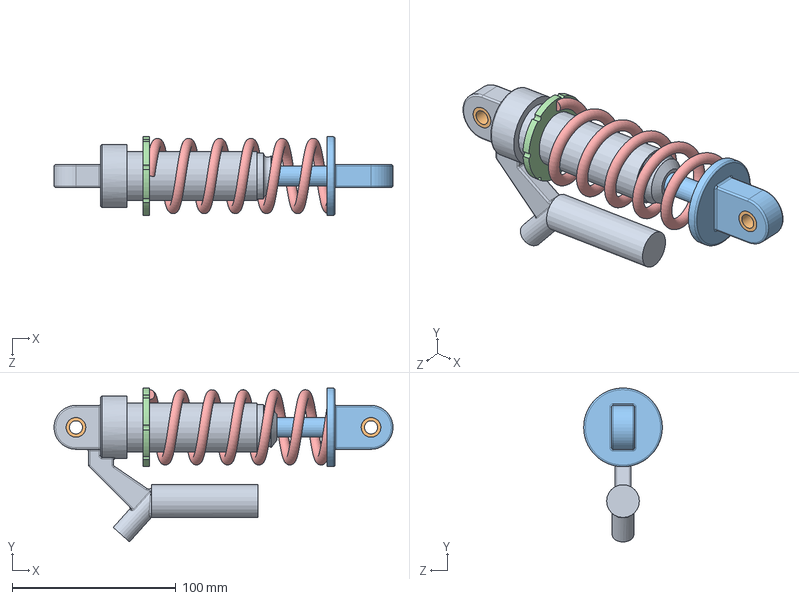
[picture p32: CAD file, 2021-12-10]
Solidworks/Suspension/SubAssemblies/Shock_Absorber_Assembly.SLDASM
206.8 x 93.9 x 48.0 mm
Outer Cylinder
bushing x 2
Piston
adjustment ring
Spring
Piston Head

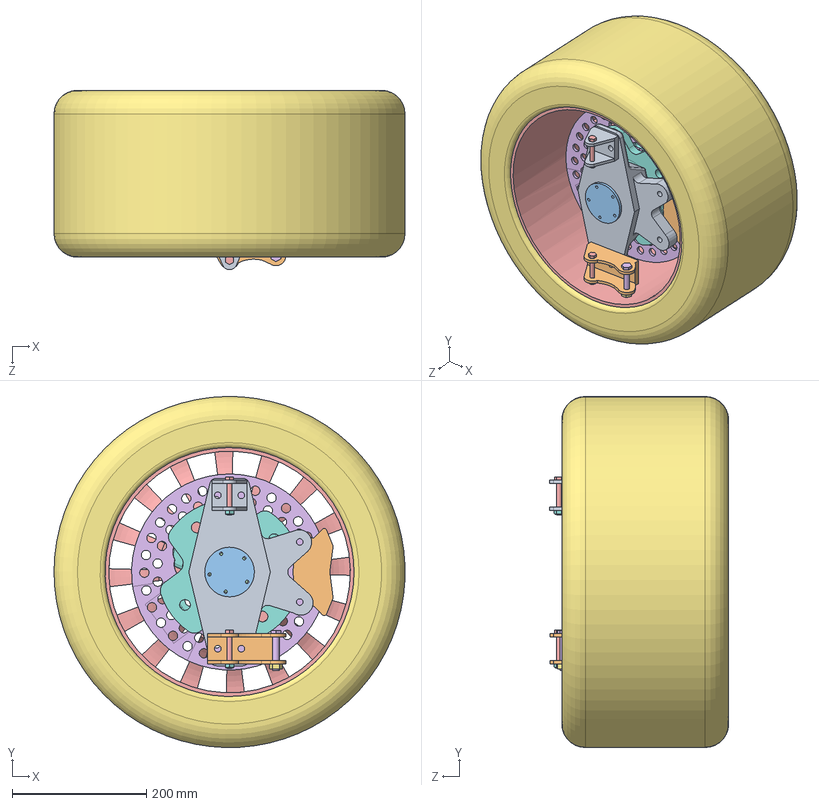
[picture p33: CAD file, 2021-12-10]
Solidworks/Wheel Knuckle Rim Mounts/Knuckle Assem-Caliper Mount/Front Left Knuckle Assembley.SLDASM
523.0 x 523.1 x 267.3 mm
Knuckle Rear
Calipers
Nut for Shaft Tires
Pads x 2
Rims
Rotor Third Time Charm
Tire
Wheel Hub 2
Top Mount 1
Bottom Mount Knuckle
Wheel Hub Shaft taper and End plate
thrust ball bearing6_ai x 2
CA_Knuckle Bolt x 2
Tie Rod Knuckle Bolt
92048A160_Center-Lock Distorted-Thread Locknuts
90101A240_18-8 Stainless Steel Thin Nylon-Insert Locknut x 2

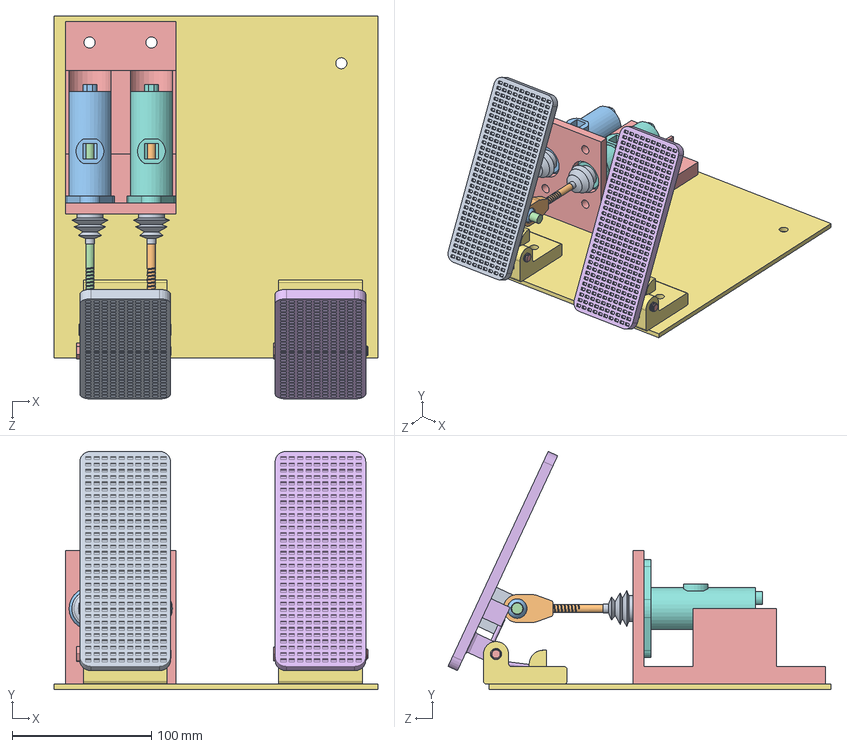
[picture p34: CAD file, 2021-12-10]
Solidworks/Pedal Box/Pedal Box Assembly.SLDASM
232.0 x 170.8 x 274.6 mm
Brake Pedal
MC rod end housing x 2
MC rod end bearing x 2
Balance Bar Brakes
Pivot Pin x 2
Torsional Spring x 2
Throttle Pedal Base Plate x 2
Master Cylinder Front
Buffer x 2
Front Piston
Master Cylinder Rear
Rear Piston
Brake MC Mount
Pedal
Base Plate

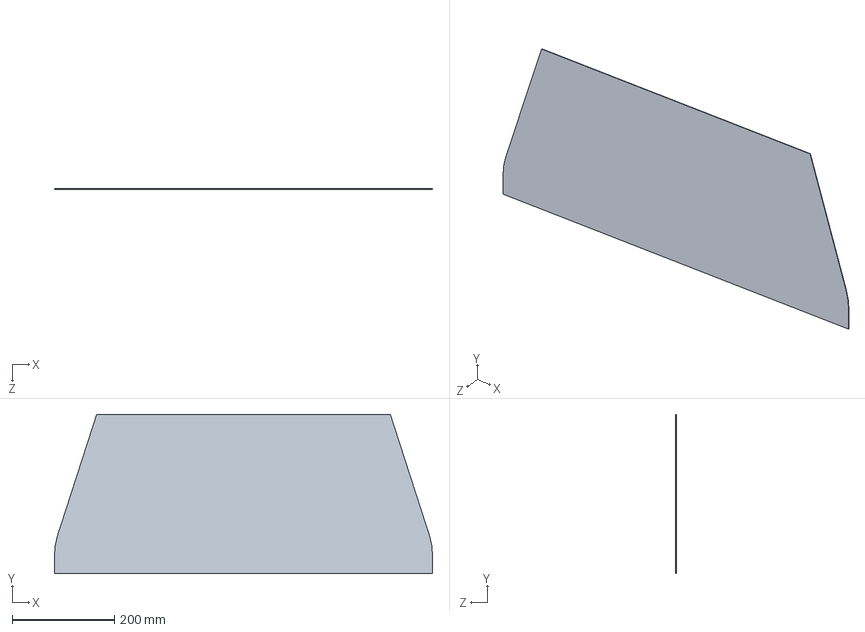
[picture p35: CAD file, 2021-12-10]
Solidworks/Plates and Firewall/Top Main Hoop Firewall.SLDPRT
740.0 x 312.0 x 1.00 mm

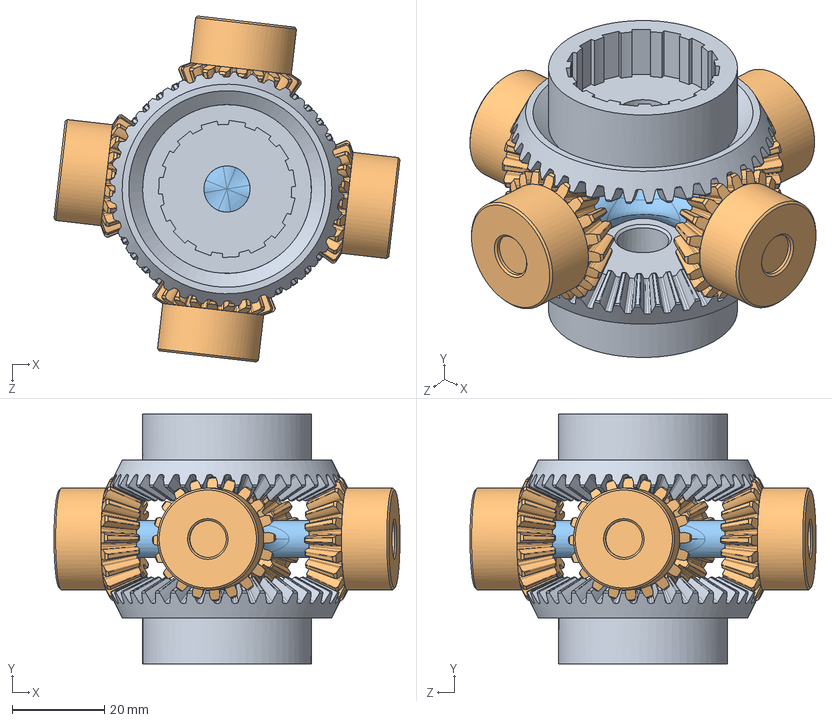
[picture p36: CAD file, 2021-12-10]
Solidworks/Powertrain/Differential/Differential_Gears_Assembly.SLDASM
74.9 x 54.1 x 74.9 mm
Bevel_Gear x 2
Spider_Gear x 4
Spider_Pin

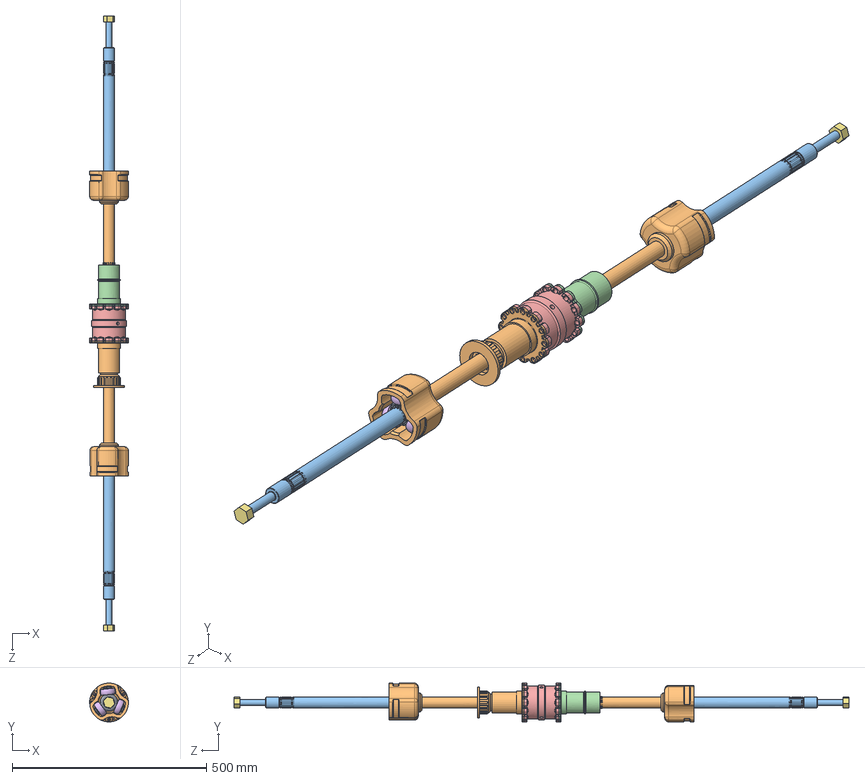
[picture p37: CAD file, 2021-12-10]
Solidworks/Powertrain/Motor_Rear_Axle_Assembly.SLDASM
100.0 x 100.0 x 1582.6 mm
Tripod_Spider x 2
Tripod_Shaft x 2
Half_Axle_Shaft x 2
Needles x 6
RE x 6
Roller x 6
Bevel_Gear x 2
Spider_Gear x 4
Spider_Pin
Sprocket_Diff_Housing
Clutch_Plate x 10
Output_Housing
Housing_Middle
thrust ball bearing3_68_am
Rim_Nut x 2

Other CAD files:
Solidworks/Steering/Updated Steering/Steering Wheel/Test Chassis Assembley With Steering.SLDASM
Solidworks/Suspension/SubAssemblies/RLCARight_Assembly.SLDASM
Solidworks/Wheel Knuckle Rim Mounts/Knuckle Assem-Caliper Mount/Rear Knuckle Assembley Final.SLDASM
Solidworks/Pedal Box/Rod End Assembley.SLDASM
Solidworks/Battery/Battery Mount.SLDPRT
Solidworks/Battery/Battery_Assembly.SLDASM
Solidworks/Battery/Battery_Casing.SLDPRT
Solidworks/Battery/Battery_Cell.SLDPRT
Solidworks/Battery/Battery_Cover.SLDPRT
Solidworks/Battery/Battery_Stack.SLDASM
Solidworks/Battery/Battery_Stack_Housing.SLDPRT
Solidworks/Battery/Battery_Stack_Pad.SLDPRT
Solidworks/Battery/Conduction_Plate.SLDPRT
Solidworks/Battery/Fan.SLDPRT
Solidworks/Battery/Slave Board.SLDPRT
Solidworks/Chassis with Panels.SLDPRT
Solidworks/Front Wing/Bottom Plate.SLDPRT
Solidworks/Front Wing/Chassis Front Wing Bottom Mount.SLDPRT
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

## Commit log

2021-12-04 add log function, add steering
2021-12-09 add chassis calculations
2021-12-09 steering wip
2021-12-09 fix steering file
2021-12-09 finish steering equations
2021-12-10 add solidworks parts
    [5905K132_Needle-Roller Bearing.SLDPRT, 90045A116_Top-Lock Distorted-Thread Locknut.SLDPRT, 90101A240_18-8 Stainless Steel Thin Nylon-Insert Locknut.SLDPRT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]
2021-12-10 para test
2021-12-10 pull grabcad
    [Battery Mount.SLDPRT, Battery_Assembly.SLDASM, Battery_Casing.SLDPRT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]
2021-12-10 readme and excel
    [Modelling and Analysis Calculations FSAE02.xlsx, Suspension Force Calc.xlsx]
